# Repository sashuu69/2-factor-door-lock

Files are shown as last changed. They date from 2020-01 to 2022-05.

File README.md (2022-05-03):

# 2 Factor Authenticated Door Lock

## Introduction

The 2 Factor door lock is a locking system built using Arduino UNO, LCD display, R307 fingerprint sensor and keypad.

## Folder Structure

1. docs/top-layer.png : PCB Board top Design
2. docs/bottom-layer.png : PCB Board bottom design
3. docs/drills.png : PCB Board drills design
4. eagle-design : PCB design
5. src : code

## Components Used

1. Switch (X1) - [Tomson Electronics](https://www.tomsonelectronics.com/products/6mm-x-6mm-x-5mm-micro-switch)
2. LED 0805 (x3) - [Digikey](https://www.digikey.in/catalog/en/partgroup/chipled-0805-rectangle-with-flat-top-leds/34905)
3. Pin header (x2) - [Robu](https://robu.in/product/adafruit-stacking-headers-for-feather-12-pin-and-16-pin-female-headers/)
4. Screw Terminal 1x2 (x1) - [Tomson Electronics](https://www.tomsonelectronics.com/products/2-pin-pcb-mount-screw-terminal-block-connectors-126)
5. Screw Terminal 1x4 (x1) - [Robu](https://robu.in/product/4-pin-5-08mm-pitch-pluggable-screw-terminal-block-pack-of-3/)
6. Capacitor 0805 100nF (x1) - [Robu](https://robu.in/product/100nf-0805-surface-mount-multilayer-ceramic-capacitor-pack-of-40/)
7. Resistor 0805 100Ω (x1) - [Tomson Electronics](https://www.tomsonelectronics.com/products/4-7-820-ohms-thick-film-chip-smd-resistors-0805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)
8. Resistor 0805 10KΩ (x3) - [Tomson Electronics](https://www.tomsonelectronics.com/products/1-240-kohms-thick-film-chip-smd-resistors-0805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)
9. Capacitor 175TMP-0810 10µF (x1) - [Tomson Electronics](https://www.mouser.in/ProductDetail/Lelon/VE-100M2ATR-0810?qs=GtPRU6UQL8zXzI3APMGIww==)
10. Resistor 0805 150Ω (x1) - [ELECTRONICScomp](https://www.electronicscomp.com/150-ohm-resistor-0805-smd-package)
11. Crystal 16Hz (x1) - [Tomson Electronics](https://www.tomsonelectronics.com/products/crystal-oscillator-16-mhz-small)
12. Resistor 0805 180Ω (x1) - [Tomson Electronics](https://www.tomsonelectronics.com/products/4-7-820-ohms-thick-film-chip-smd-resistors-0805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)
13. Resistor 0805 1KΩ (x7) - [Tomson Electronics](https://www.tomsonelectronics.com/products/1-240-kohms-thick-film-chip-smd-resistors-0805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)
14. Diode 1N4007 (x2) - [Tomson Electronics](https://www.tomsonelectronics.com/products/diode-1n-4007)
15. Capacitor 175TMP-0810 1µF (x1) - [Mouser](https://www.mouser.in/ProductDetail/Lelon/VZH-331M1ETR-0810?qs=sXzuR3ywNuchKJ7mmh%252BA6w==)
16. Resistor 0805 220Ω (x3) - [Tomson Electronics](https://www.tomsonelectronics.com/products/4-7-820-ohms-thick-film-chip-smd-resistors-0805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)
17. Capacitor 0805 22pF (x1) - [Tomson Electronics](https://robu.in/product/22pf-0805-surface-mount-multilayer-ceramic-capacitor-pack-of-50/)
18. Resistor 0805 330Ω (x1) - [Tomson Electronics](https://www.tomsonelectronics.com/products/4-7-820-ohms-thick-film-chip-smd-resistors-0805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)
19. Resistor 0805 390Ω (x1) - [KTRON](https://www.ktron.in/product/resistor-390-ohms-5-1-8w-smd-0805/)
20. Capacitor 175TMP-0810 470µF (x1) - [Element14](https://in.element14.com/c/passive-components/capacitors/aluminium-electrolytic-capacitors/smd-aluminium-electrolytic-capacitors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)
21. Resistor 0805 510Ω (x1) - [Tomson Electronics](https://www.tomsonelectronics.com/products/4-7-820-ohms-thick-film-chip-smd-resistors-0805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)
22. Resistor 0805 680Ω (x1) - [ELECTRONICScomp](https://www.electronicscomp.com/680-ohm-resistor-0805-smd-package)
23. 7805T (x1) - [Tomson Electronics](https://www.tomsonelectronics.com/products/regulator-ic-7805)
24. Resistor 0805 82Ω (x1) - [KTRON](https://www.ktron.in/product/resistor-82-ohms-51-8w-smd-0805/)
25. ATMEGA328P-AU (x1) - [Tomson Electronics](https://www.tomsonelectronics.com/products/smd-ic-atmega-328?variant=49936455955)
26. BC547 (x1) - [Tomson Electronics](https://www.tomsonelectronics.com/products/transistor-bc-547)
27. Barrel Jack (x1) - [Tomson Electronics](https://www.tomsonelectronics.com/products/dc-barrel-power-jack)
28. PCF8574AT (x1) - [Mouser](https://www.mouser.in/ProductDetail/NXP-Semiconductors/PCF8574AT-3518?qs=LOCUfHb8d9s1dE4yk7F8TQ%3D%3D)
29. 5V Relay (x1) - [Tomson Electronics](https://www.tomsonelectronics.com/products/5v-single-contact-sugar-cube-relay)
30. 16x2 LCD Display (x1) - [Tomson Electronics](https://www.tomsonelectronics.com/products/16x1-character-green-backlight-lcd-display)

## PCB Design

### Top Layer

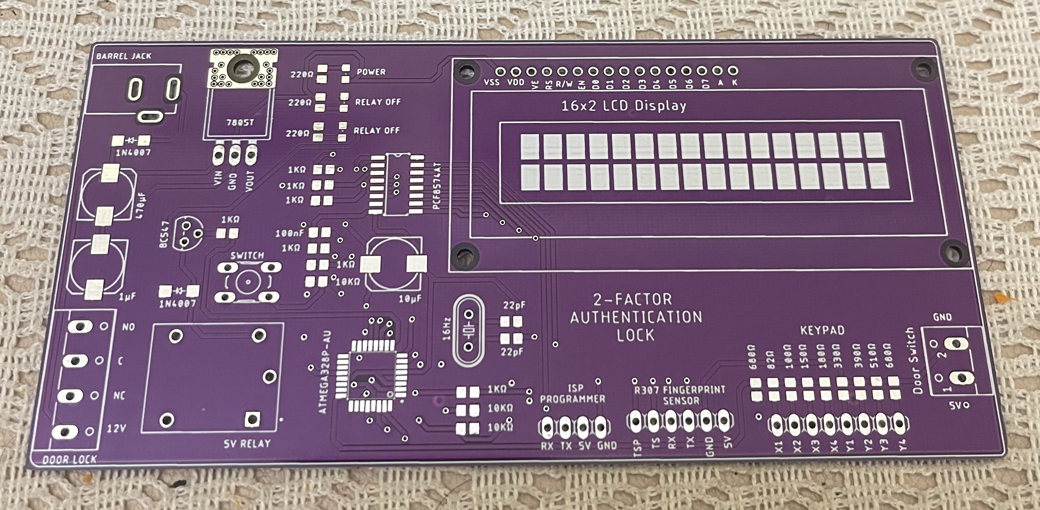
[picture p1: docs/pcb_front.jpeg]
PCB - Top


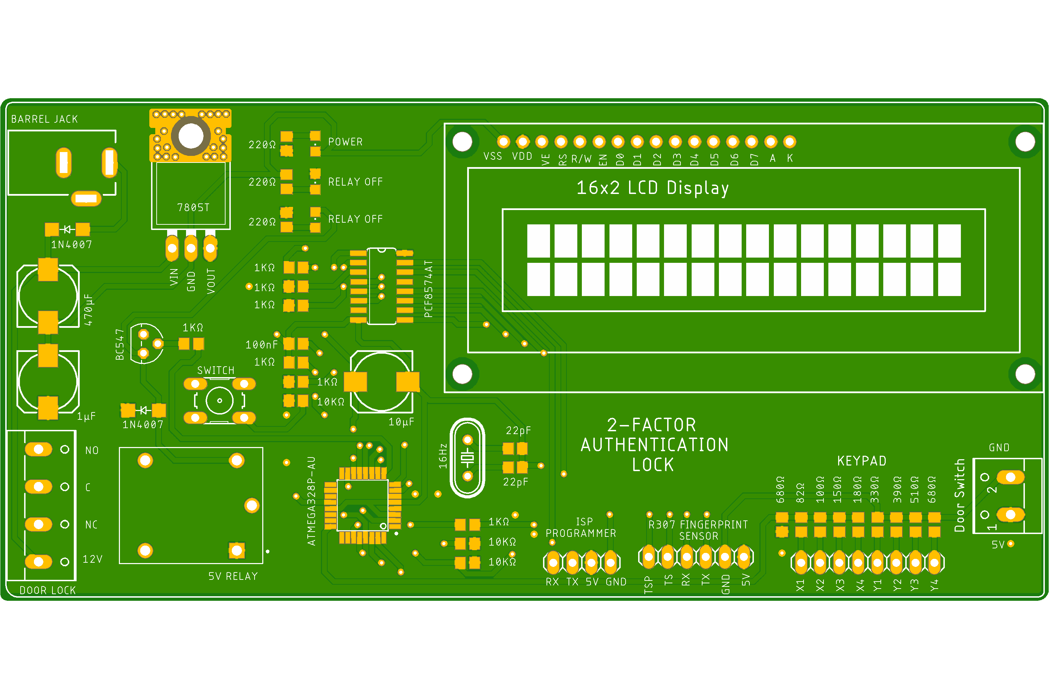
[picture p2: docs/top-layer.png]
Top layer


### Bottom Layer

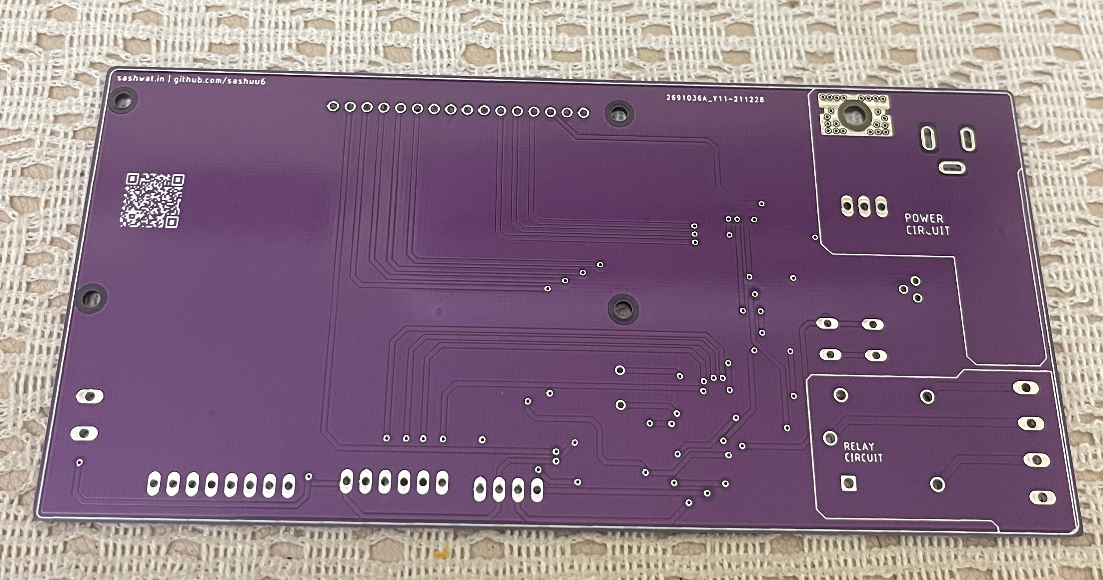
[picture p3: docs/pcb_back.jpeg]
PCB - Bottom


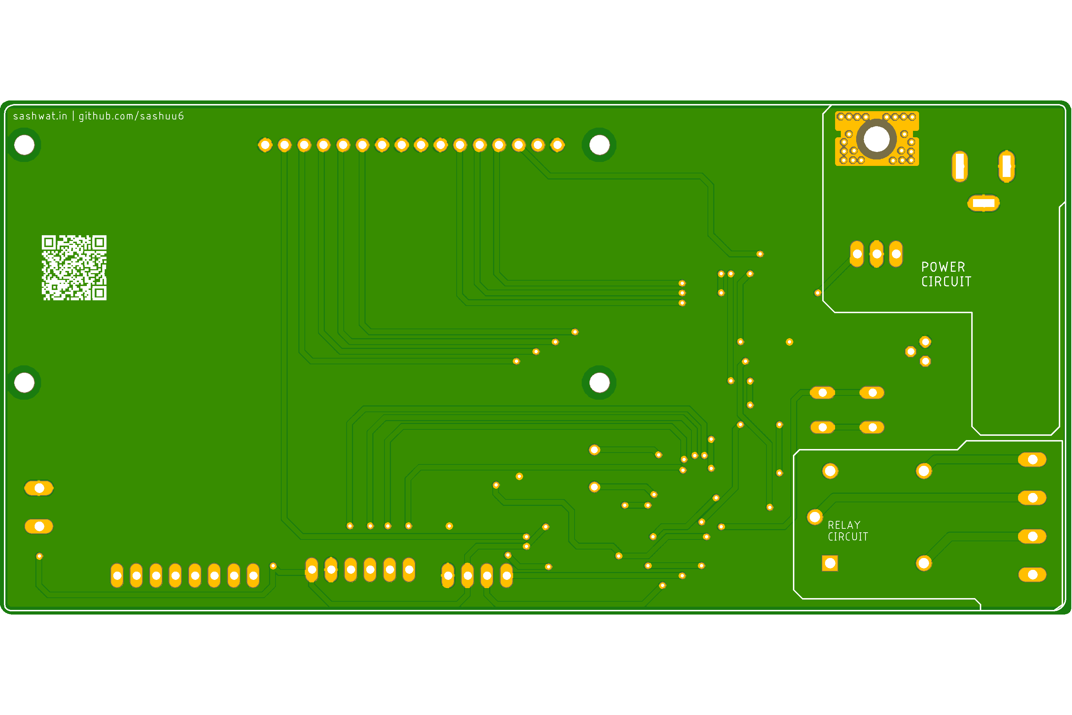
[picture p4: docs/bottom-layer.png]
Bottom layer


### Drills Design

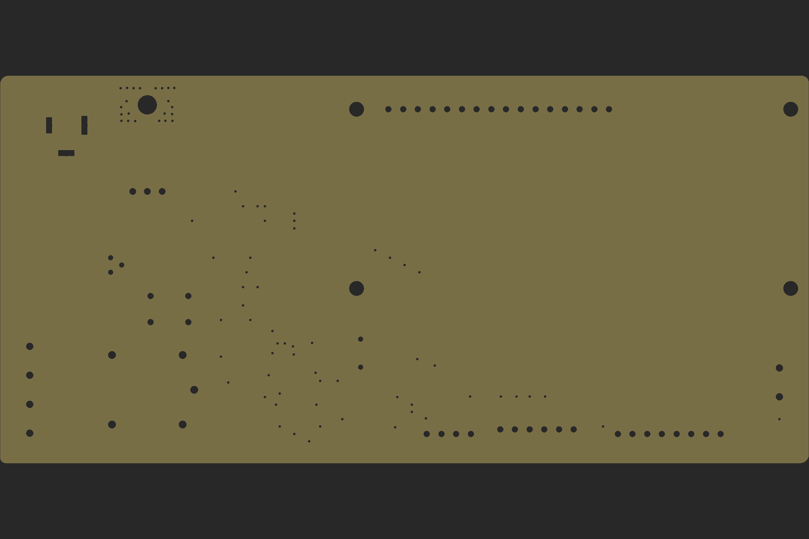
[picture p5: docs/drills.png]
Drills design


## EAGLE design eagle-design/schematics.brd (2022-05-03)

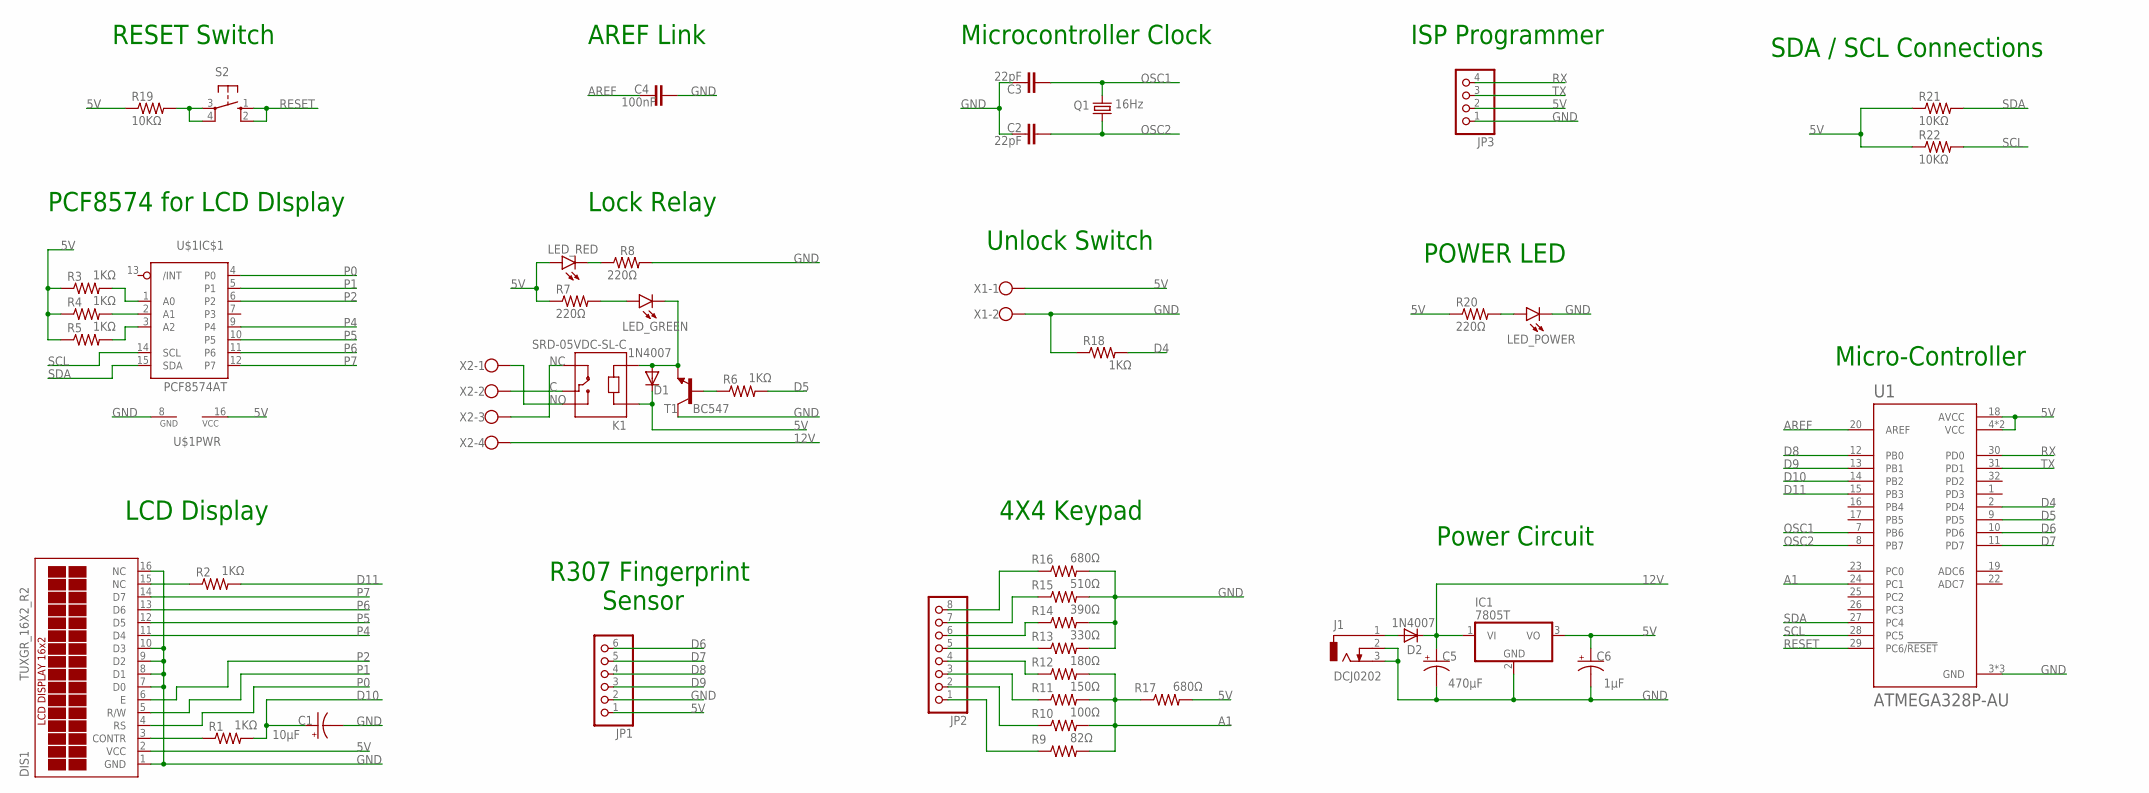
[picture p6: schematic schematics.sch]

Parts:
C1: 10µF; 175TMP-0810
C2, C3: 22pF; C0805
C4: 100nF; C0805
C5: 470µF; 175TMP-0810
C6: 1µF; 175TMP-0810
D1, D2: 1N4007; SMA
DIS1: TUXGR_16X2_R2
IC1: 7805T; TO220H
J1: DCJ0202
JP1: PINHD-1X6; 1X06
JP2: PINHD-1X8; 1X08
JP3: PINHD-1X4; 1X04
K1: SRD-05VDC-SL-C; RELAY_SRD-05VDC-SL-C
LED_GREEN: LEDCHIPLED_0805; CHIPLED_0805
LED_POWER: LEDCHIPLED_0805; CHIPLED_0805
LED_RED: LEDCHIPLED_0805; CHIPLED_0805
Q1: 16Hz; HC49/S
R1, R2, R3, R4, R5, R6, R18: 1KΩ; R0805
R7, R8, R20: 220Ω; R0805
R9: 82Ω; R0805
R10: 100Ω; R0805
R11: 150Ω; R0805
R12: 180Ω; R0805
R13: 330Ω; R0805
R14: 390Ω; R0805
R15: 510Ω; R0805
R16, R17: 680Ω; R0805
R19, R21, R22: 10KΩ; R0805
S2: 10-XX; B3F-10XX
T1: BC547; TO92
U1: ATMEGA328P-AU; QFP80P900X900X120-32N
U$1: PCF8574AT; SO16
X1: W237-102
X2: W237-4

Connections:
5V: C6.+, D1.K (C), DIS1.2 (VCC), IC1.3 (VO), JP1.1, JP3.2, K1.A1, LED_RED.A, R3.1, R4.1, R5.1, R7.1, R17.2, R19.1, R20.1, R21.1, R22.1, U1.4 (VCC), U1.6 (VCC), U1.18 (AVCC), U$1.16 (VCC), X1.1
12V: C5.+, D2.K (C), IC1.1 (VI), X2.4
A1: R9.2, R10.2, R11.2, R12.2, R17.1, U1.24 (PC1)
AREF: C4.2, U1.20 (AREF)
C: K1.COM, X2.2
D4: R18.2, U1.2 (PD4)
D5: R6.2, U1.9 (PD5)
D6: JP1.6, U1.10 (PD6)
D7: JP1.5, U1.11 (PD7)
D8: JP1.4, U1.12 (PB0)
D9: JP1.3, U1.13 (PB1)
D10: C1.+, R1.2, U1.14 (PB2)
D11: R2.2, U1.15 (PB3)
GND: C1.-, C2.2, C3.2, C4.1, C5.-, C6.-, DIS1.1 (GND), DIS1.7 (D0), DIS1.8 (D1), DIS1.9 (D2), DIS1.10 (D3), DIS1.16 (NC), IC1.2 (GND), J1.2, J1.3, JP1.2, JP3.1, LED_POWER.C, R8.2, R13.2, R14.2, R15.2, R16.2, R18.1, T1.3 (C), U1.3 (GND), U1.5 (GND), U1.21 (GND), U$1.8 (GND), X1.2
unnamed: DIS1.3 (CONTR), R1.1
unnamed: R3.2, U$1.1 (A0)
unnamed: R4.2, U$1.2 (A1)
unnamed: DIS1.15 (NC), R2.1
unnamed: R5.2, U$1.3 (A2)
unnamed: D1.A, K1.A2, LED_GREEN.C, T1.1 (E)
unnamed: R6.1, T1.2 (B)
unnamed: LED_RED.C, R8.1
unnamed: LED_GREEN.A, R7.2
unnamed: JP2.8, R16.1
unnamed: JP2.7, R15.1
unnamed: JP2.6, R14.1
unnamed: JP2.5, R13.1
unnamed: JP2.4, R12.1
unnamed: JP2.3, R11.1
unnamed: JP2.2, R10.1
unnamed: JP2.1, R9.1
unnamed: R19.2, S2.3, S2.4 (P1)
unnamed: LED_POWER.A, R20.2
unnamed: D2.A, J1.1
NC: K1.NC, X2.3
NO: K1.NO, X2.1
OSC1: C3.1, Q1.2, U1.7 (PB6)
OSC2: C2.1, Q1.1, U1.8 (PB7)
P0: DIS1.4 (RS), U$1.4 (P0)
P1: DIS1.5 (R/W), U$1.5 (P1)
P2: DIS1.6 (E), U$1.6 (P2)
P4: DIS1.11 (D4), U$1.9 (P4)
P5: DIS1.12 (D5), U$1.10 (P5)
P6: DIS1.13 (D6), U$1.11 (P6)
P7: DIS1.14 (D7), U$1.12 (P7)
RESET: S2.1 (S), S2.2 (S1), U1.29 (PC6/!RESET)
RX: JP3.4, U1.30 (PD0)
SCL: R22.2, U1.28 (PC5), U$1.14 (SCL)
SDA: R21.2, U1.27 (PC4), U$1.15 (SDA)
TX: JP3.3, U1.31 (PD1)

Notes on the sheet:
LCD Display
PCF8574 for LCD DIsplay
R307 Fingerprint Sensor
Lock Relay
4X4 Keypad
Unlock Switch
RESET Switch
Microcontroller Clock
AREF Link
ISP Programmer
POWER LED
Power Circuit
Micro-Controller
SDA / SCL Connections

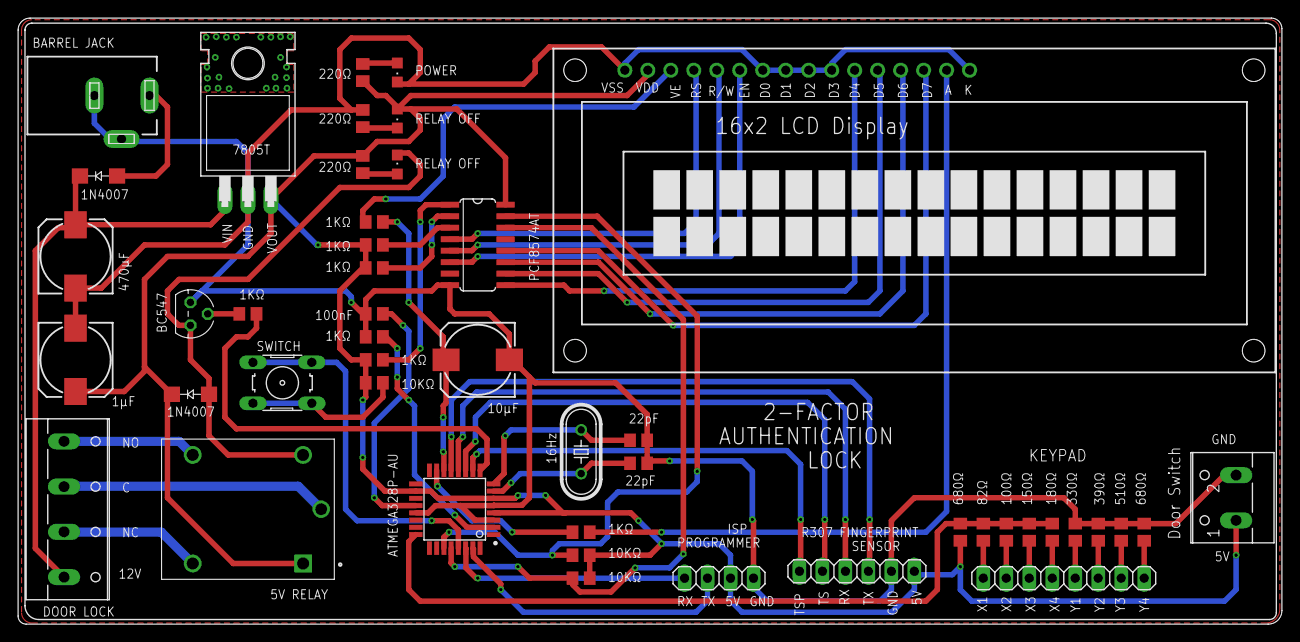
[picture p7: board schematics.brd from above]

Board: 2 copper layers, 139.7 x 67.0 mm, 47 parts (0 on the bottom side), 50 nets.

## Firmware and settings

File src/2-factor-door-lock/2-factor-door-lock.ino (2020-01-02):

/*
                              $$\                            $$$$$$\  
                              $$ |                          $$  __$$\ 
  $$$$$$$\  $$$$$$\   $$$$$$$\ $$$$$$$\  $$\   $$\ $$\   $$\ $$ /  \__|
$$  _____| \____$$\ $$  _____|$$  __$$\ $$ |  $$ |$$ |  $$ |$$$$$$$\  
\$$$$$$\   $$$$$$$ |\$$$$$$\  $$ |  $$ |$$ |  $$ |$$ |  $$ |$$  __$$\ 
  \____$$\ $$  __$$ | \____$$\ $$ |  $$ |$$ |  $$ |$$ |  $$ |$$ /  $$ |
$$$$$$$  |\$$$$$$$ |$$$$$$$  |$$ |  $$ |\$$$$$$  |\$$$$$$  | $$$$$$  |
\_______/  \_______|\_______/ \__|  \__| \______/  \______/  \______/

 * Project Name: 2 Factor Door Lock
 * Repository link: https://github.com/sashuu6/2-factor-door-lock
 * Developed by: Sashwat K
 * Created on: 1 Jan 2020
 * Last Modified: 2 Jan 2020
 * Revision: 2
*/

#include <LiquidCrystal_I2C.h> // LCD Library
#include <Adafruit_Fingerprint.h> // R307 Library
#include <Keypad.h> // Keypad Library


LiquidCrystal_I2C lcd(0x3F,20,4); // LCD

// R307 fingerprint sensor
SoftwareSerial mySerial(2, 3);
Adafruit_Fingerprint finger = Adafruit_Fingerprint(&mySerial);
uint8_t id;

// Keypad 4 * 3
const byte ROWS = 4; //four rows
const byte COLS = 3; //three columns
char keys[ROWS][COLS] = {
  {'1','2','3'},
  {'4','5','6'},
  {'7','8','9'},
  {'*','0','#'}
};
byte rowPins[ROWS] = {10, 9, 8, 7}; //connect to the row pinouts of the keypad
byte colPins[COLS] = {6,5,4}; //connect to the column pinouts of the keypad

Keypad keypad = Keypad( makeKeymap(keys), rowPins, colPins, ROWS, COLS );

// Functions
void dashboard();
uint8_t resetFingerprint();
int verifyFingerprint();

long passCode = 0;
int temp,n;
long correctPassCode = 963258;
long resetPin = 742690;

void setup() {
  // put your setup code here, to run once:
  Serial.begin(9600); //Serial printing
  Serial.println("2-Factor Door lock");
  Serial.println("By Sashwat K");
  Serial.println("Checkut www.sashwat.in");
  
  //Welcome Screen
  lcd.init();
  lcd.backlight();
  lcd.setCursor(1,0);
  lcd.print("2-Factor");
  lcd.setCursor(6,1);
  lcd.print("Door Lock");
  delay(1000);
  lcd.clear();
  lcd.setCursor(1,0);
  lcd.print("By,");
  lcd.setCursor(6,1);
  lcd.print("Sashwat K");
  delay(1000);

  // Initialising fingerprint sensor
  lcd.clear();
  lcd.setCursor(0,0);
  lcd.print("Booting sensors");
  lcd.setCursor(0,1);
  lcd.print("Please Wait...");
  finger.begin(57600);
  delay(500);

  // Verifying Fingerprint Sensr
  if (finger.verifyPassword()) {
    Serial.println("Found fingerprint sensor!");
  } 
  else {
    Serial.println("Did not find fingerprint sensor :(");
    lcd.clear();
    lcd.setCursor(0,0);
    lcd.print("sensor error..");
    while (1) { delay(1); }
  }
}

void loop() {
  // put your main code here, to run repeatedly:
  dashboard();
  n = 0;
  char key = keypad.getKey();
  if (key) {
    if (key == '*') {
      Serial.println("Reset Fingerprint..");
      while (!resetFingerprint() );
    }
  }

  if (verifyFingerprint() >= 100) {
    Serial.println("Sucess");
    lcd.clear();
    lcd.setCursor(0,0);
    lcd.print("Fingerprint");
    lcd.setCursor(0,1);
    lcd.print("Verified..");
    delay(1000);
    lcd.clear();
    lcd.setCursor(0, 0);
    lcd.print("Level - 2");
    delay(1000);
    lcd.clear();
    lcd.setCursor(0, 0);
    lcd.print("Enter passcode: ");
    lcd.setCursor(0, 1);
    
    while(true) {
      int i=0;
      char key2 = keypad.getKey();
      if (key2) {
        if (key2 == '#') {
          passCode = 0;
          n = 0;
          lcd.clear();
          lcd.setCursor(0, 0);
          lcd.print("Cleared..");
          delay(500);
          lcd.clear();
          lcd.setCursor(0, 0);
          lcd.print("Enter passcode: ");
        }
        else if(key2 == '*') {
          if(passCode == correctPassCode) {
            lcd.clear();
            lcd.setCursor(0, 0);
            lcd.print("Access granted");
            Serial.println("Access granted");
            delay(2000);
            passCode = 0;
            i = 0;
            break;
          }
          else {
            lcd.clear();
            lcd.setCursor(0, 0);
            lcd.print("Access denied");
            Serial.println("Access denied");
            delay(1000);
            passCode = 0;
            i = 0;
            break;
          }
        }
        else {
          temp = key2 - '0';
          passCode = (passCode * 10) + temp;
          n++;
          lcd.clear();
          lcd.setCursor(0, 0);
          lcd.print("Enter passcode: ");
          lcd.setCursor(0, 1);
          while(i<n) {
            lcd.print("*");
            i++;
          }
        }
      }
    }
  }  
  delay(500);
}

void dashboard() {
  lcd.clear();
  lcd.setCursor(0,0);
  lcd.print("Level - 1");
  lcd.setCursor(0,1);
  lcd.print("Place finger..");
}

uint8_t resetFingerprint() {
  int p = -1;
  Serial.println("Resetting fingerprint");
  lcd.clear();
  lcd.setCursor(0,0);
  lcd.print("Resetting");
  lcd.setCursor(0,1);
  lcd.print("Fingerprint..");
  delay(1500);
  lcd.clear();
  lcd.setCursor(0, 0);
  lcd.print("Enter passcode: ");
  while(true) {
    int i=0;
    char key = keypad.getKey();
    if (key) {
      if (key == '#') {
        passCode = 0;
        n = 0;
        lcd.clear();
        lcd.setCursor(0, 0);
        lcd.print("Cleared..");
        delay(500);
        lcd.clear();
        lcd.setCursor(0, 0);
        lcd.print("Enter passcode: ");
      }
      else if(key == '*') {
        if(passCode == resetPin) {
          lcd.clear();
          lcd.setCursor(0, 0);
          lcd.print("Fingerprint");
          lcd.setCursor(0, 1);
          lcd.print("change granted");
          Serial.println("Fingerprint change granted");
          delay(2000);
          passCode = 0;
          i = 0;
          break;
        }
        else {
          lcd.clear();
          lcd.setCursor(0, 0);
          lcd.print("Fingerprint");
          lcd.setCursor(0, 1);
          lcd.print("change denied");
          Serial.println("Fingerprint change denied");
          delay(1000);
          passCode = 0;
          i = 0;
          n = 0;
          return -1;
          break;
        }
      }
      else {
        temp = key - '0';
        passCode = (passCode * 10) + temp;
        n++;
        lcd.clear();
        lcd.setCursor(0, 0);
        lcd.print("Enter passcode: ");
        lcd.setCursor(0, 1);
        while(i<n) {
          lcd.print("*");
          i++;
        }
      }
    }
  }
  Serial.println("Place finger");
  lcd.clear();
  lcd.setCursor(0,0);
  lcd.print("Place");
  lcd.setCursor(0,1);
  lcd.print("Finger..");
  while (p != FINGERPRINT_OK) {
    p = finger.getImage();
    switch (p) {
    case FINGERPRINT_OK:
      Serial.println("Image taken");
      lcd.clear();
      lcd.setCursor(0,0);
      lcd.print("Scanning");
      lcd.setCursor(0,1);
      lcd.print("Finger..");
      break;
    case FINGERPRINT_NOFINGER:
      Serial.println(".");
      break;
    case FINGERPRINT_PACKETRECIEVEERR:
      Serial.println("Communication error");
      lcd.clear();
      lcd.setCursor(0,0);
      lcd.print("Error");
      break;
    case FINGERPRINT_IMAGEFAIL:
      Serial.println("Imaging error");
      lcd.clear();
      lcd.setCursor(0,0);
      lcd.print("Error");
      break;
    default:
      Serial.println("Unknown error");
      lcd.clear();
      lcd.setCursor(0,0);
      lcd.print("Error");
      break;
    }
  }

  p = finger.image2Tz(1);
  switch (p) {
    case FINGERPRINT_OK:
      Serial.println("Image converted");
      break;
    case FINGERPRINT_IMAGEMESS:
      Serial.println("Image too messy");
      lcd.clear();
      lcd.setCursor(0,0);
      lcd.print("Error");
      return p;
    case FINGERPRINT_PACKETRECIEVEERR:
      Serial.println("Communication error");
      lcd.clear();
      lcd.setCursor(0,0);
      lcd.print("Error");
      return p;
    case FINGERPRINT_FEATUREFAIL:
      Serial.println("Could not find fingerprint features");
      lcd.clear();
      lcd.setCursor(0,0);
      lcd.print("Error");
      return p;
    case FINGERPRINT_INVALIDIMAGE:
      Serial.println("Could not find fingerprint features");
      lcd.clear();
      lcd.setCursor(0,0);
      lcd.print("Error");
      return p;
    default:
      Serial.println("Unknown error");
      lcd.clear();
      lcd.setCursor(0,0);
      lcd.print("Error");
      return p;
  }

  Serial.println("Remove finger");
  lcd.clear();
  lcd.setCursor(0,0);
  lcd.print("Remove finger");
  delay(2000);
  lcd.clear();
  lcd.setCursor(0,0);
  lcd.print("Place finger");
  p = 0;
  while (p != FINGERPRINT_NOFINGER) {
    p = finger.getImage();
  }
  p = -1;
  Serial.println("Place same finger again");
  while (p != FINGERPRINT_OK) {
    p = finger.getImage();
    switch (p) {
    case FINGERPRINT_OK:
      Serial.println("Image taken");
      break;
    case FINGERPRINT_NOFINGER:
      Serial.print(".");
      break;
    case FINGERPRINT_PACKETRECIEVEERR:
      Serial.println("Communication error");
      lcd.clear();
      lcd.setCursor(0,0);
      lcd.print("Error");
      break;
    case FINGERPRINT_IMAGEFAIL:
      Serial.println("Imaging error");
      lcd.clear();
      lcd.setCursor(0,0);
      lcd.print("Error");
      break;
    default:
      Serial.println("Unknown error");
      lcd.clear();
      lcd.setCursor(0,0);
      lcd.print("Error");
      break;
    }
  }

  // OK success!

  p = finger.image2Tz(2);
  switch (p) {
    case FINGERPRINT_OK:
      Serial.println("Image converted");
      break;
    case FINGERPRINT_IMAGEMESS:
      Serial.println("Image too messy");
      lcd.clear();
      lcd.setCursor(0,0);
      lcd.print("Error");
      return p;
    case FINGERPRINT_PACKETRECIEVEERR:
      Serial.println("Communication error");
      lcd.clear();
      lcd.setCursor(0,0);
      lcd.print("Error");
      return p;
    case FINGERPRINT_FEATUREFAIL:
      Serial.println("Could not find fingerprint features");
      lcd.clear();
      lcd.setCursor(0,0);
      lcd.print("Error");
      return p;
    case FINGERPRINT_INVALIDIMAGE:
      Serial.println("Could not find fingerprint features");
      lcd.clear();
      lcd.setCursor(0,0);
      lcd.print("Error");
      return p;
    default:
      Serial.println("Unknown error");
      lcd.clear();
      lcd.setCursor(0,0);
      lcd.print("Error");
      return p;
  }
  
  // OK converted!
  
  p = finger.createModel();
  if (p == FINGERPRINT_OK) {
    Serial.println("Prints matched!");
  } else if (p == FINGERPRINT_PACKETRECIEVEERR) {
    Serial.println("Communication error");
    lcd.clear();
    lcd.setCursor(0,0);
    lcd.print("Error");
    return p;
  } else if (p == FINGERPRINT_ENROLLMISMATCH) {
    Serial.println("Fingerprints did not match");
    lcd.clear();
    lcd.setCursor(0,0);
    lcd.print("Error");
    return p;
  } else {
    Serial.println("Unknown error");
    lcd.clear();
    lcd.setCursor(0,0);
    lcd.print("Error");
    return p;
  }   
  
  p = finger.storeModel(1);
  if (p == FINGERPRINT_OK) {
    Serial.println("Stored!");
    lcd.clear();
    lcd.setCursor(0,0);
    lcd.print("Stored..");
  } else if (p == FINGERPRINT_PACKETRECIEVEERR) {
    Serial.println("Communication error");
    lcd.clear();
    lcd.setCursor(0,0);
    lcd.print("Error");
    return p;
  } else if (p == FINGERPRINT_BADLOCATION) {
    Serial.println("Could not store in that location");
    lcd.clear();
    lcd.setCursor(0,0);
    lcd.print("Error");
    return p;
  } else if (p == FINGERPRINT_FLASHERR) {
    Serial.println("Error writing to flash");
    lcd.clear();
    lcd.setCursor(0,0);
    lcd.print("Error");
    return p;
  } else {
    Serial.println("Unknown error");
    lcd.clear();
    lcd.setCursor(0,0);
    lcd.print("Error");
    return p;
  }
}

int verifyFingerprint() {
  uint8_t p = finger.getImage();
  if (p != FINGERPRINT_OK)  return -1;

  p = finger.image2Tz();
  if (p != FINGERPRINT_OK)  return -1;

  p = finger.fingerFastSearch();
  if (p != FINGERPRINT_OK)  return -1;
  
  return finger.confidence; 
}

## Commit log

2020-01-01 Fixed errors and commented the header files
    [2-factor-door-lock.ino]
2020-01-03 new changes
    [2-factor-door-lock.fzz]
2021-08-26 created new eagle schematics
    [2-factor-door-lock.fzz, schematics.sch]
2021-08-28 completed design
    [schematics.brd, schematics.sch]
2021-08-28 Added component list with links
    [schematics.brd]
2021-08-28 Added missing connection
    [schematics.brd]
2021-08-28 Added new exports
    [schematics.brd]
2022-05-03 Added PCB photos
    [schematics.brd]
